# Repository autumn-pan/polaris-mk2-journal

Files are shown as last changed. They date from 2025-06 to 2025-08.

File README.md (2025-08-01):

# Lepton Rocket
The Lepton Rocket is a TVC rocket that is capable of guiding itself using its thruster, as well as vertical landing using a second thruster. It requires no parachute or fins and is capable of self-stabilization using only gimballed motors and lands propulsively.

# Motivation
Our motivation for building this rocket stems from a deep passion for model rocketry and a will to learn and improve through this project. Building such a complicated rocket not only helps us learn and grow as people but also pushes technological boundaries we face today with innovative new solutions. Every step, from Kalman filters to thrust vectoring, offers unique challenges that serve as learning experiences. We hope that our work will go on to support other aspiring rocketeers through open sourcing and tutorials. Moreover, we are testing new methods of reversing exhaust jets and are testing materials in extreme environments. We hope that this research will inspire other projects that can make a real impact.

# Design
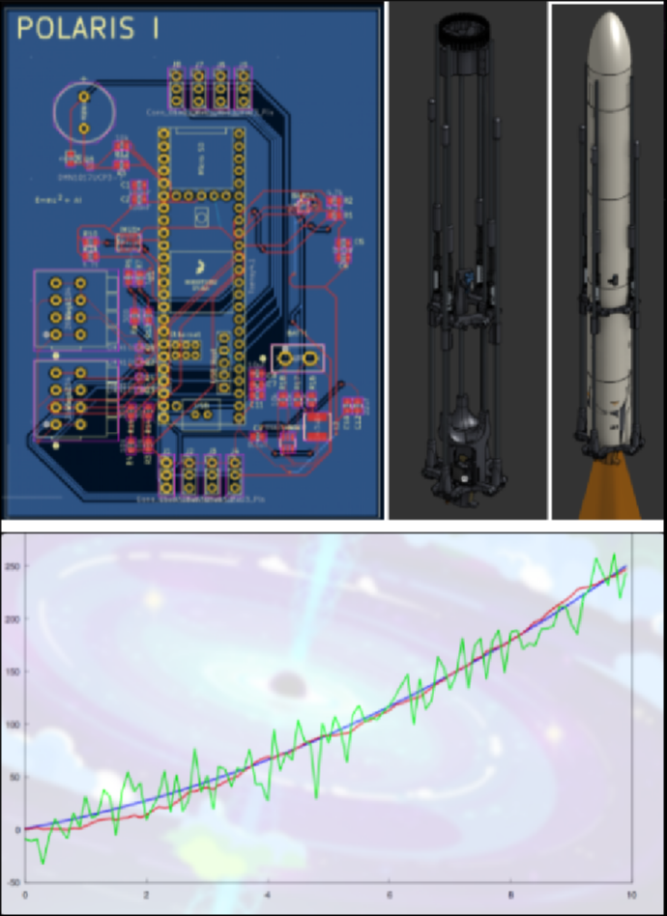
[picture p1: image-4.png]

PCB
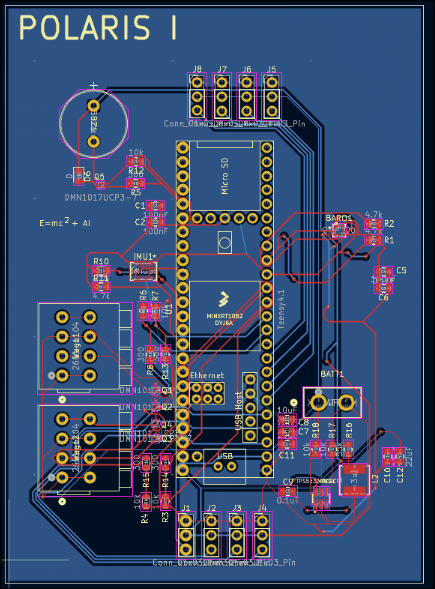
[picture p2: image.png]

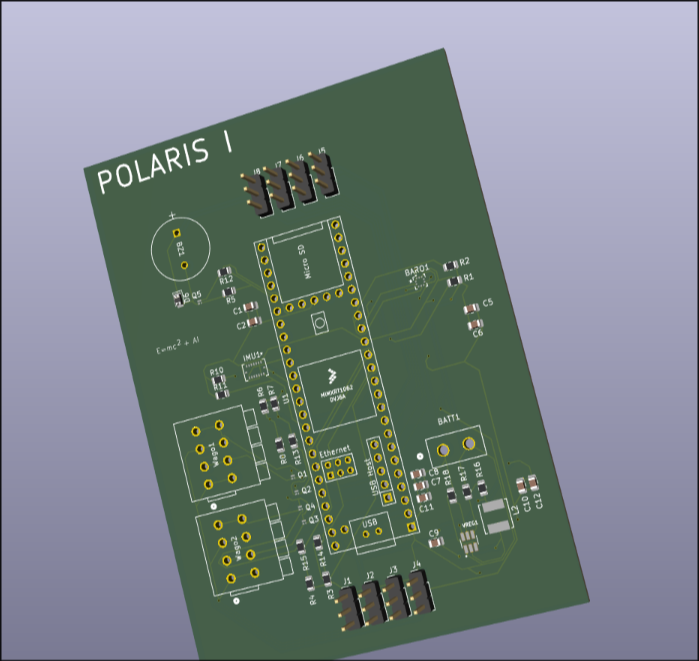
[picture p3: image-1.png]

WIRING
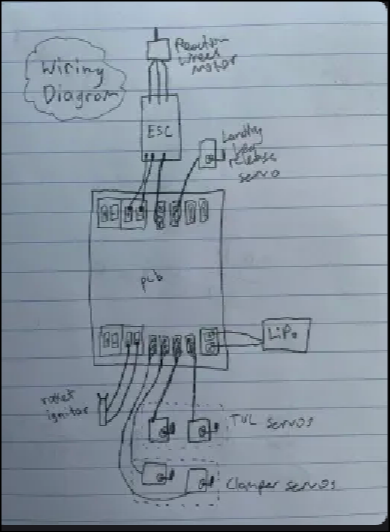
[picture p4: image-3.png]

CAD


# CAD Files
View the CAD files in ./cad, or preferably in the onshape document
[Link](https://cad.onshape.com/documents/b936ec593d2f13f8b4301d6a/w/959d82f8ce1a388125efc6ac/e/d0e27454aa34d56363c8f698)
# BOM -- Total Cost: $288.5, $307.25 after tax
| Name | Cost | Link | Purpose |
|---|---|---|---|
| Teensy 4.1 | 35.49  | [Link](https://www.amazon.com/PJRC-Cortex-M7-Processor-iMXRT1062-Without/dp/B088JY7P2H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) | Processing information and running code |
| Bosch Sensortec BMI088 | 5.23 | [Link](https://www.digikey.com/en/products/detail/bosch-sensortec/BMI088/8634936) | Reading inertial data |
| Bosch Sensortec BMP390 | 3.15 | [Link](https://www.digikey.com/en/products/detail/bosch-sensortec/BMP390/16164577) | Reading altitude |
| 2 WAGOs  (2601-1104) | 8.72 | [Link](https://www.digikey.com/en/products/detail/wago-corporation/2601-1104/17123797?gQT=1) | Connecting pyro channels |
| XT30U connector | 0.72 | [Link](https://www.tme.eu/en/details/xt30upb-m/dc-power-connectors/amass/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) | Connecting the battery |
| 8x Servo Pins (G800W305018EU) | 7.84 | [Link](https://www.digikey.com/en/products/detail/amphenol-icc-commercial-products-/G800W305018EU/13683151?gQT=1) | Connecting the servo pins |
| 5x DMN1019UVT-7 | 4.10 | [Link](https://www.digikey.com/en/products/detail/diodes-incorporated/DMN1019UVT-7/5126835) | Controlling pyro channels |
| Printed Circuit Board | 50.00  | [Link](https://jlcpcb.com/) | Mounting flight computer devices on. We only ask that you pay for printing, shipping, and taxes on the raw circuit boards. We will try to fund the resistors, capacitors, etc. ourselves |
| 3ml Syringes | 2.93  | [Link](https://www.aliexpress.us/item/3256806328171497.html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) | Dampening landing legs |
| Brushless Motor | 0.99 | [Link](https://www.aliexpress.us/item/3256806626806030.html?) | Driving the reaction wheel |
| Extension Cable | 5.99 | [Link](https://www.amazon.com/FLY-RC-Connector-Extension-Brushless/dp/B0B12CFKNZ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) | Connecting the motor to the flight computer |
| Set Screws 50pc 2cm 5mm | 1.38 | [Link](https://www.aliexpress.us/item/2251832795980382.html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) | Weighing down the reaction wheel |
| 1/4 acetyl copolymer rods-- 4 3ft rods and 8 2ft rods| 36.91 | https://buyplastic.com/delrin-acetal-copolymer-plastic-rod/ | Landing legs and supporting the fuselage
|2 servos bms127wv+| 54.97|[link](https://www.redwingrc.com/product.php?productid=2746)| Pricy, but very necessary due to the high forces that they will be subjected to. These are for tvc
| 2 servos PTK 7462W MG| 19.44 | https://www.aliexpress.us/item/3256807624830309.html? | Thrust reversal system
| TSP563200DDCR | 0.90 | https://www.digikey.com/en/products/detail/texas-instruments/TPS563200DDCR/5034343 | converting the battery to a lower voltage for the teensy to handle
| 5x 300 Ohm Resistor RC0402JR-07300RL| 0.50 | https://www.digikey.com/en/products/detail/yageo/RC0402JR-07300RL/726461 | Managing MOSFET gates
| 7x 10k Ohm Resistor RC0402JR-0710KL| 0.70 | https://www.digikey.com/en/products/detail/yageo/RC0402JR-0710KL/726418 | Pull down resistors for MOSFETS
| 4x 4.7k Ohm Resistor RC0402JR-074K7L | 0.50 | https://www.digikey.com/en/products/detail/yageo/RC0402JR-074K7L/726477 | Sensor stack pull down resistors
| 1x 55k Ohm Resistor ERA-2AEB563X| 0.10 | https://www.digikey.com/en/products/detail/panasonic-electronic-components/ERA-2AEB563X/1706047 | Managing TSP563200 output voltage
| 7x 0.1 uF Capacitor CL05B104KP5NNNC | 0.56 | https://www.digikey.com/en/products/detail/samsung-electro-mechanics/CL05B104KP5NNNC/3886660 | smoothing voltage
| 2x 22 uF Capacitor | 0.05 | https://www.digikey.com/en/products/detail/murata-electronics/GRM188R61A226ME15D/5027561 | Smoothing voltage with the TSP
| F15-0 Estes Rocket Motor| 22.95 | https://fusionscalehobbies.com/products/estes-f15-0-29mm-engines-2pk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 | Launching the rocket |
|Solder paste | 4.36 | https://www.aliexpress.us/item/3256809207808464.html? | soldering SMDs to the PCB |
| Threaded inserts | 1.73 | https://www.aliexpress.us/item/3256803396040989.html? | TVC assembly |
| Bearings | 6.26 | https://www.aliexpress.us/item/3256802138888272.html? | TVC Assembly |
| 5x Threaded acrew | 7.05 | https://www.aliexpress.us/item/3256806603708402.html? | General connections |
| Insert Nuts | 4.98 | https://www.aliexpress.us/item/3256808011211144.html? | General connections |

Notes on our vendors:
- Teensy 4.1 is necessary for its high speed, reliability, and ease of use. It is necessary for advanced avionics like this project. However, it's difficult to optimize the price of, and the cheapest price from a trusted vendor was about $31. Considering free shipping however, the cheapest vendor was on Amazon and was $35. Aliexpress was thoroughly considered and while vendors there were considered, they were found to be misleading and/or untrustworthy. A bad MPU is not only a waste of money and time, but can also be a violation of safety guidelines.
- The acetyl copolymer rods are the cheapest and most reliable on the market for what they are-- we thoroughly checked. Aliexpress does not offer any rod long enough to support this rocket, and has insufficient quality assurance which could compromise the safety of this project. Also note that this is including shipping for a large object, which is absolutely necessary in this case. Alternative rocket bodies can cost upwards of $90 at this size, so this really is the cheapest possible. Furthermore, we considered carbon fiber rods from aliexpress, however we were not allowed to purchase them in the quantity that we needed, and even the cheapest rods from Aliexpress did not make a significant difference. We really optimized the rods and rocket body to the extreme.
- We looked on Aliexpress for banana extender cables, but all options were either more expensive or significantly too short for what we needed. The one on amazon is the cheapest one that works.
- The servos we found are the only servos strong enough that can fit inside the rocket. Any larger servos could introduce significant problems during flight. These are also necessary because it is for a guidance system, and therefore needs to be fast and respond quickly. We found the cheapest servos possible.
- The servos for thrust reversing can be cheaper, so we got the cheapest servos from Aliexpress that are still strong enough to do their job. This cut costs by upwards of $40. The servos could not be cheaper than this.
- We were promised that Hack Club would supply one pack of Estes F15-0 motors by Acon
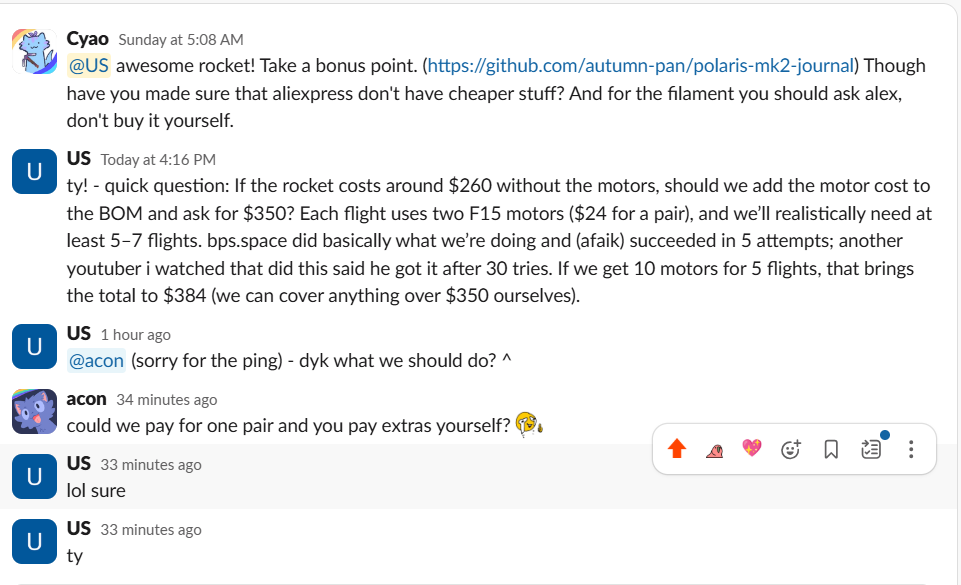
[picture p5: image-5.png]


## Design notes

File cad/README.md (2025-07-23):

Link to the Onshape:
[Link](https://cad.onshape.com/documents/b936ec593d2f13f8b4301d6a/w/959d82f8ce1a388125efc6ac/e/d0e27454aa34d56363c8f698)

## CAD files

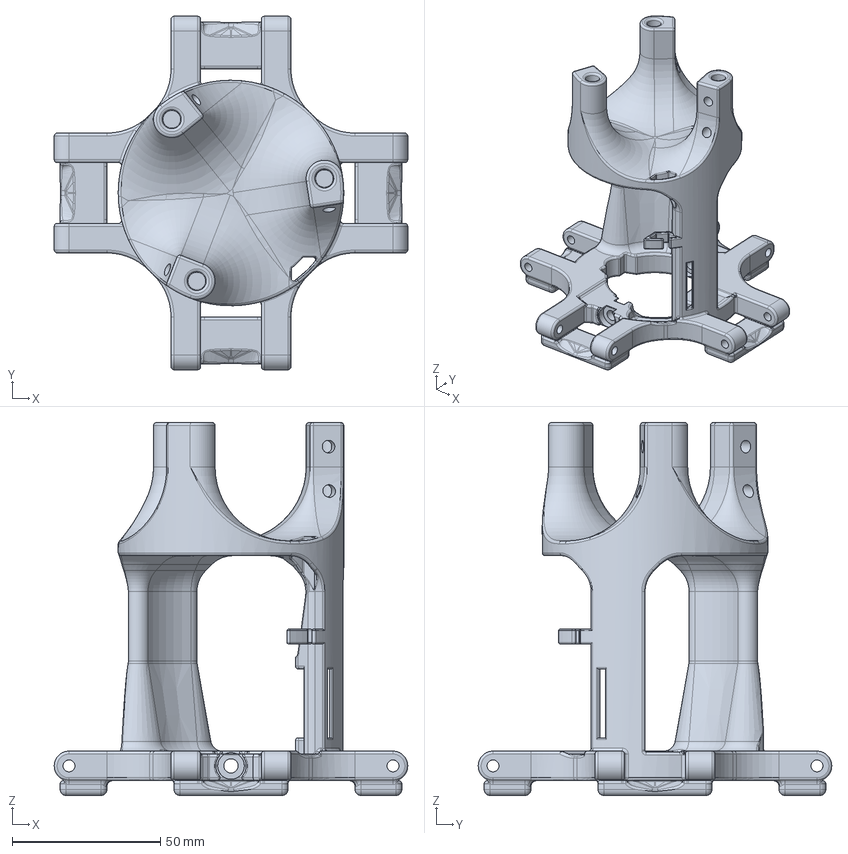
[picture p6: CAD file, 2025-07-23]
cad/Assembly - Outside.step
119.4 x 119.4 x 126.0 mm

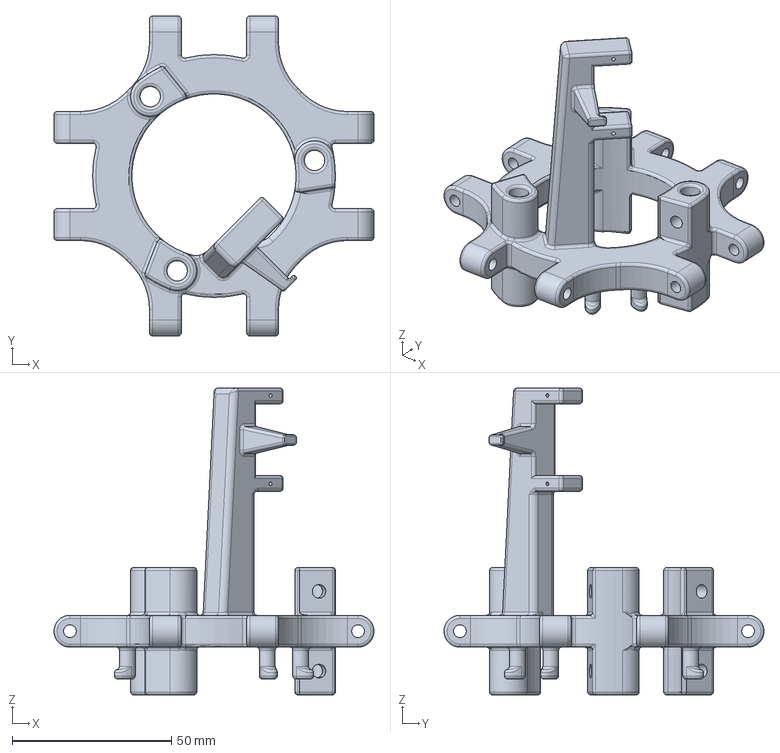
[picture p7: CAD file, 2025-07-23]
cad/Assembly - Part 23.step
100.4 x 100.4 x 96.3 mm

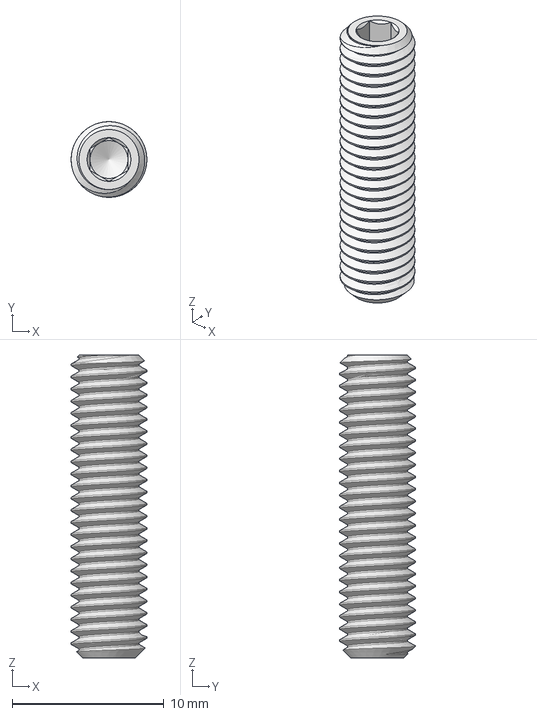
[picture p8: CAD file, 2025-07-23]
cad/Assembly - Part 1 (36).step
5.00 x 5.00 x 20.0 mm

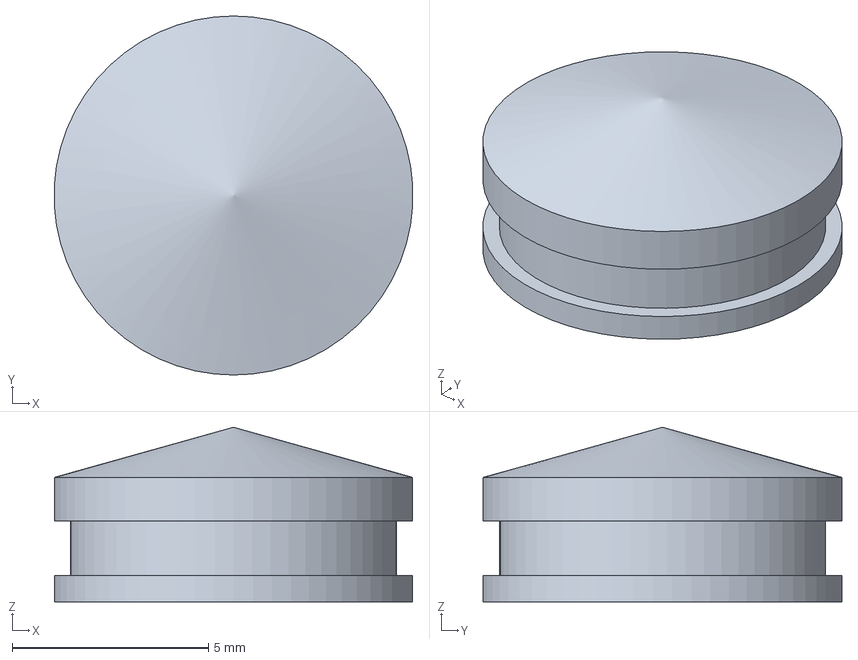
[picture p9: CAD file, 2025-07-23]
cad/Assembly - 7510A651_Plastic Syringe (11).step
9.13 x 9.14 x 4.45 mm

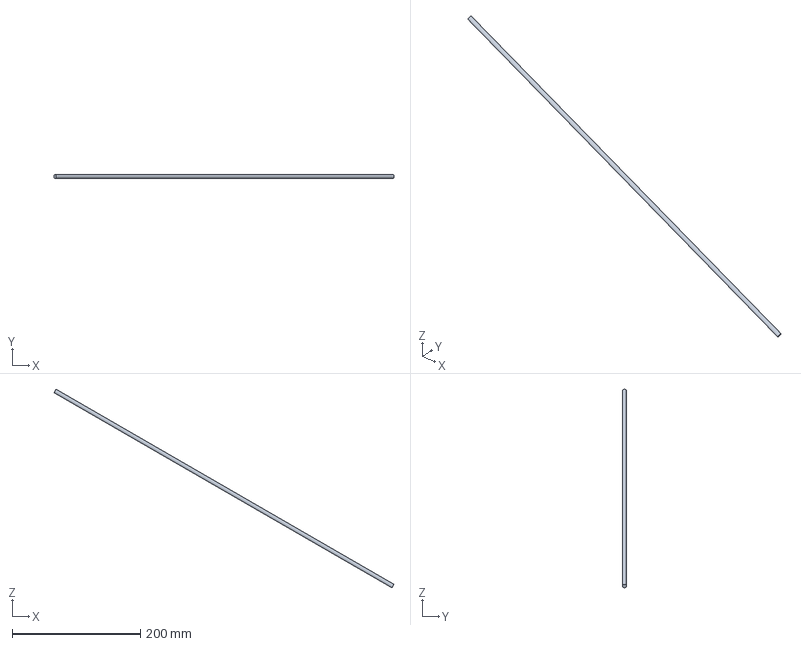
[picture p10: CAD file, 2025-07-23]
cad/Assembly - Part 21.step
531.1 x 6.35 x 310.3 mm

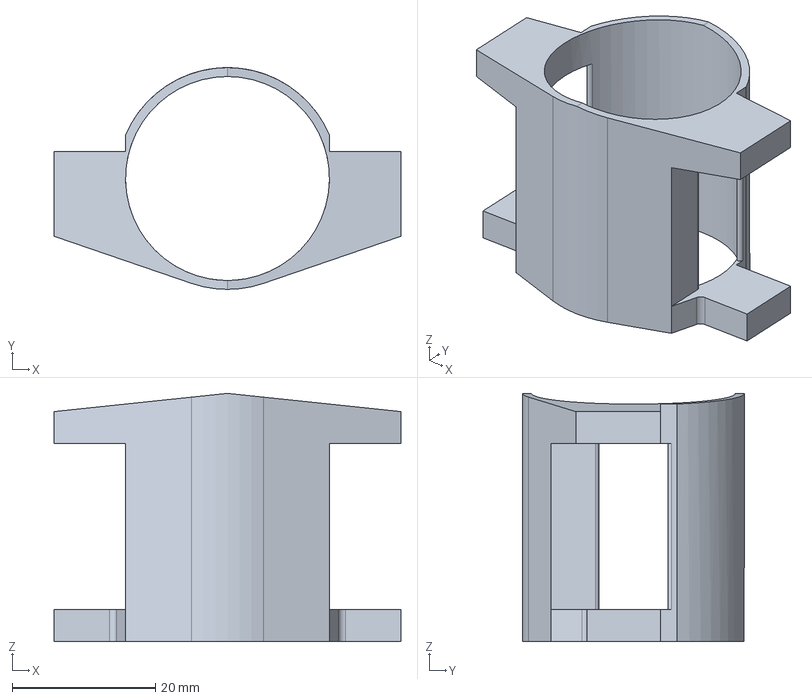
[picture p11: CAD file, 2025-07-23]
cad/Assembly - Part 8.step
48.5 x 31.0 x 34.7 mm

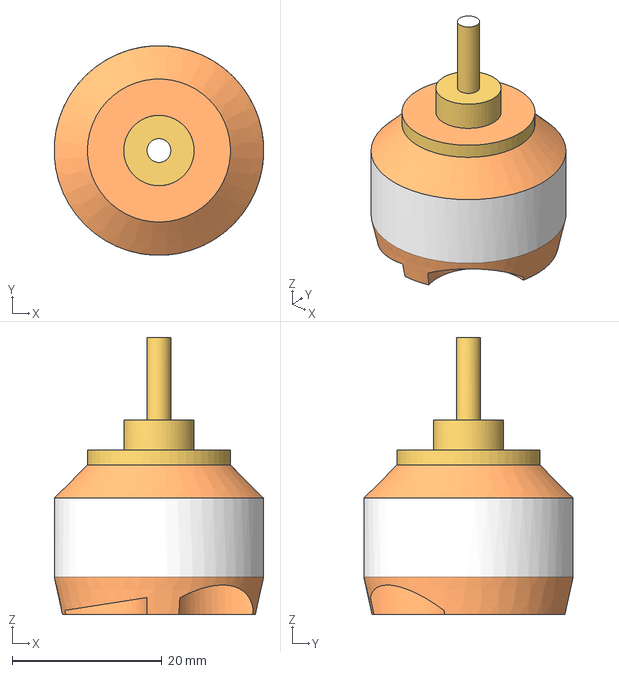
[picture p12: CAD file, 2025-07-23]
cad/Assembly - DYS D2822 2282 1100KV 1450KV 1800KV 2600KV Brushess Motor.step
28.0 x 28.0 x 37.0 mm

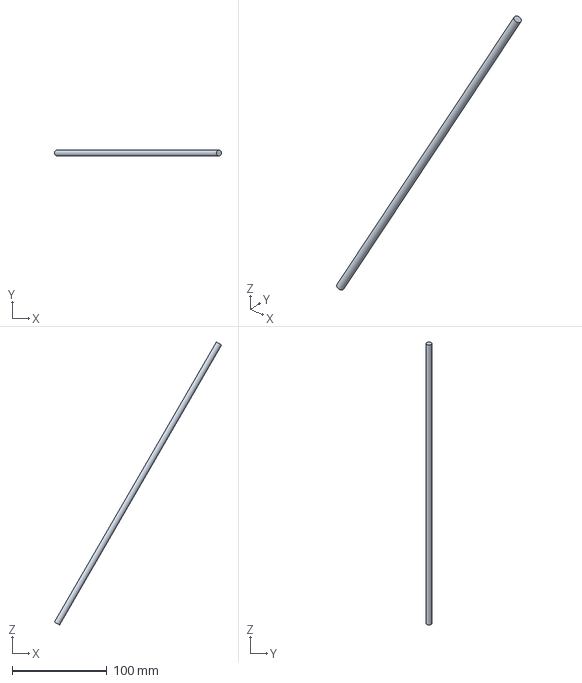
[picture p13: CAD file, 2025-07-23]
cad/Assembly - Part 26.step
176.5 x 6.35 x 298.8 mm

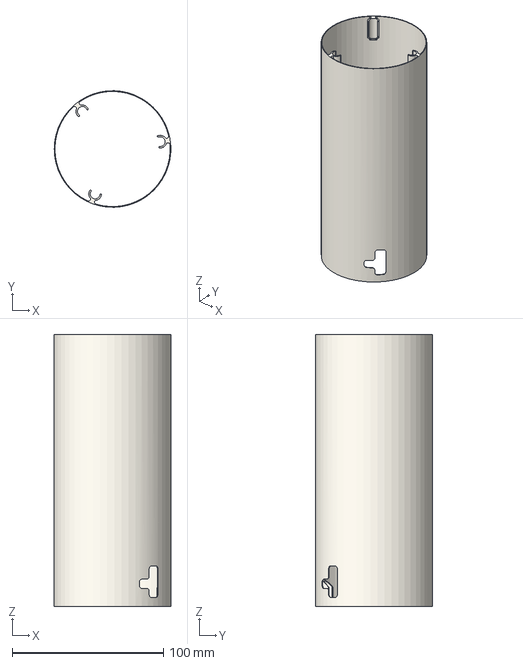
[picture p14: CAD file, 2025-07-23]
cad/Assembly - Part 31.step
77.1 x 77.2 x 180.0 mm

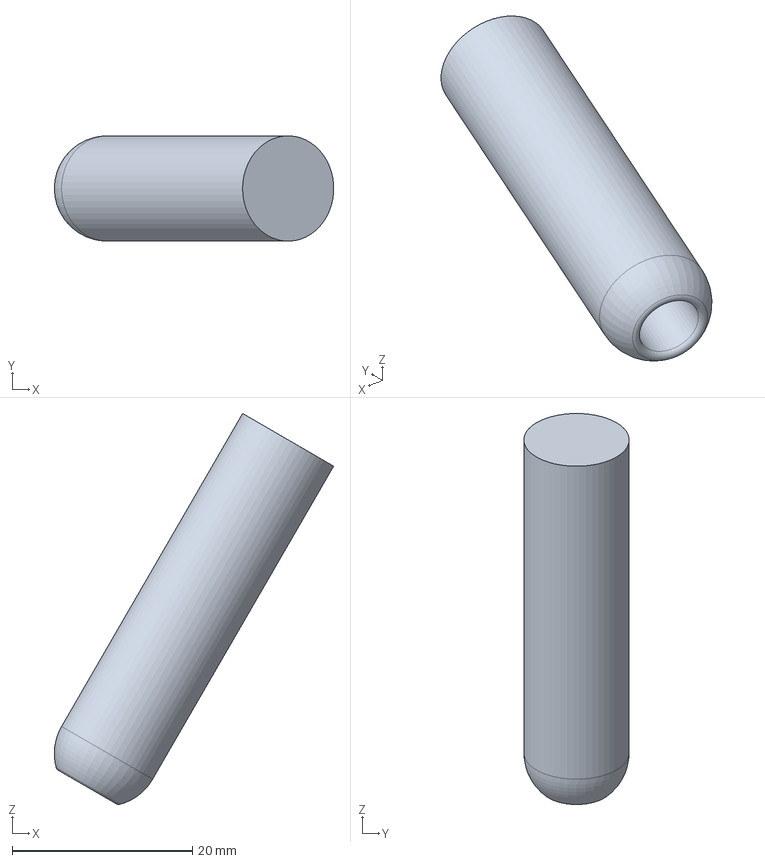
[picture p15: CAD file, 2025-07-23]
cad/Assembly - Part 25.step
31.0 x 11.7 x 43.4 mm

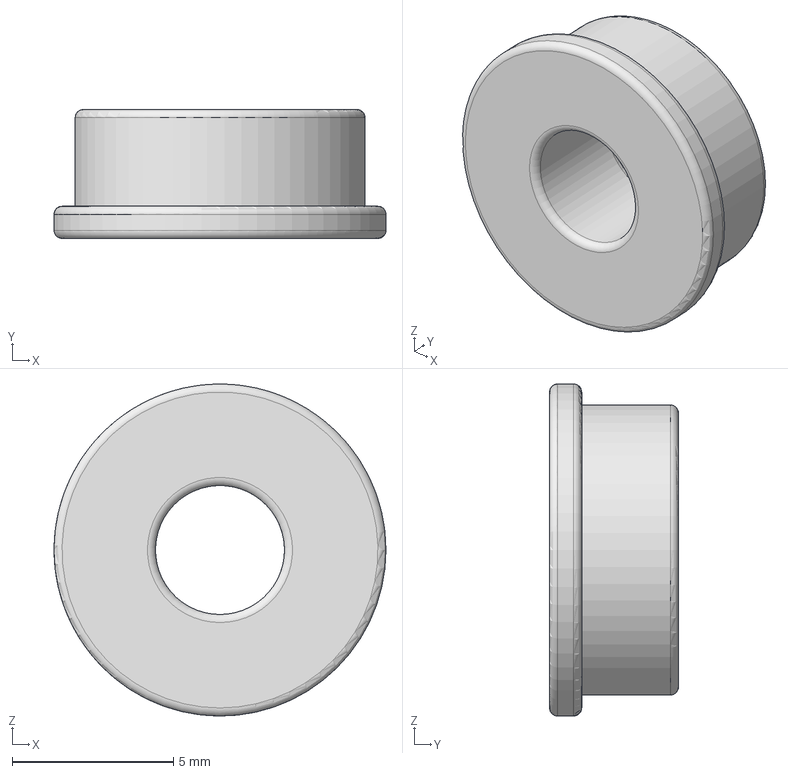
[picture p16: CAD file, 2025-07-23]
cad/Assembly - Bearing.step
10.3 x 4.00 x 10.3 mm

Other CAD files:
cad/Assembly - Part 1 (28).step
cad/Assembly - Part 1 (20).step
cad/Assembly - Part 1 (33).step
cad/Assembly - Part 1 (26).step
cad/Assembly - Part 1.step
cad/Assembly - Part 1 (27).step
cad/Assembly - Part 1 (29).step
cad/Assembly - 7510A651_Plastic Syringe (1).step
cad/Assembly - 7510A651_Plastic Syringe (10).step
cad/Assembly - 7510A651_Plastic Syringe (2).step
cad/Assembly - 7510A651_Plastic Syringe (3).step
cad/Assembly - 7510A651_Plastic Syringe (4).step
cad/Assembly - 7510A651_Plastic Syringe (5).step
cad/Assembly - 7510A651_Plastic Syringe (6).step
cad/Assembly - 7510A651_Plastic Syringe (7).step
cad/Assembly - 7510A651_Plastic Syringe (8).step
cad/Assembly - 7510A651_Plastic Syringe (9).step
cad/Assembly - 7510A651_Plastic Syringe.step
cad/Assembly - BMS-127WV (1).step
cad/Assembly - BMS-127WV (2).step
cad/Assembly - BMS-127WV.step
cad/Assembly - Bearing (1).step
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

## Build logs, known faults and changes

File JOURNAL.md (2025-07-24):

---
title: "Lepton Rocket"
author: "Umit Selvitopu/Autumn Pan"
description: "An F-Class propulsively landing rocket"
created_at: "2025-5-21"
---

Autumn Pan -- Lepton Rocket Logs -- Approx 104 hours
PCB, Code, and Design

# Day 0, May 21
When the rocket lands, it may still have a lot of kinetic energy, which is why we need landing legs with shock absorbers. Today we discussed what shock absorbers to purchase and settled on ones from McMaster.

I read through kalmanfiltertutorial among other sites to gain a rough understand of a kalman filter, which will be used later on to sort out sensor noise. I was walked through the alpha-beta-gamma filter and learned about multivariate gaussians. It was quite challenging to understand, but a kalman filter is essentially a recursive algorithm that takes the weighted average of different equations and sensor readings to determine to the best of its ability, the state of your rocket.
Time spent: 4hr
# Day 1 May 22
Before I work on Polaris Mk. 2, the flight computer on the actual rocket, I want to create the groundwork for this project by first writing a simpler flight computer so that I can better plan for this one. I initialized a PlatformIO project and imported the necessary libraries. I started out by removing unnecessary code from main.cpp. Then, I imported the BMP390 Barometer and BMI088 IMU. These two sensors will be used to find the position, velocity, and orientation of the rocket, which is important for nearly every maneuver. Of course, sensors aren't perfect so I'll have to implement something called a Kalman filter later on. I finished a very primitive version of a sensor handler class. Total time spent: 1hr
# Day 2 May 24
The first thing I did today was finish up implementing the barometer so that I could measure altitude. This also requires sea level atmospheric pressure to calculate, which varies from place to place. I decided to have it stored dynamically rather than hardcoded. A pyro channel is a pin meant to ignite a pyrotechnic device, which usually require higher voltages. I created a PyroChannel class that can fire a pyro channel for some duration, which can be used for things like parachute deployment or a second stage. I researched the Arduino SD library so that I could implement an SD card class for logging information, like sensor readings. Also, I realized that I should be storing the values of the sensors each cycle rather than directly getting them from the sensors because its more efficient, so I switched to that. Total time spent: 2.5 hrs
# Day 3 May 25
One of the bigger changes I made today was completely overhauling the SDCard class into the Logger class, which is now capable of organizing logs, along with other capabilities. I added header guards to Pyro.h to prevent any redefinition errors because I forgot to add them yesterday. I also realized that I forgot to license my work, so I did so under the MIT license. I also added a class to handle keeping track of time, which offers utils like last cycle time and elapsed time. TIme spent: 1.5 hrs
# Day 4 May 26
This was the day when I finally implemented the Kalman filter. So, when you try to use sensors, they will always have some amount of noise which can give you innaccurate readings. The goal of the kalman filter is to minimize this noise as much as possible to create the most accurate guess of the rocket's state as possible. I implemented this by using the C++ Eigen library for linear algebra and following the kalman filter equations. I derived my own state transisiton matrix, which essentially integrated acceleration and velocity. I decided not to kalman filter my gyros because I thought that it would be uneccesary for such a short flight and would increase cycle time. Then, I merged this branch into main. Total time spent: 4 hrs
# Day 5 May 27
Today I began testing for my kalman filter. I used my statesim project, which modeled kinematics and sensor noise, to test this. I imported my kalman filter and deps, then I learned and installed matplotplusplus to graph the information. Immediately, I found that my kalman filter did not function correctly and outputted nan, which I fixed by removing some zeroes from the covariant matrices. Next, the kalman filter was off by orders of magnitude, which was the result of an upside-down state transition matrix. Finally, I managed to get it to work at just over 50% reduced noise compared to raw sensor data.

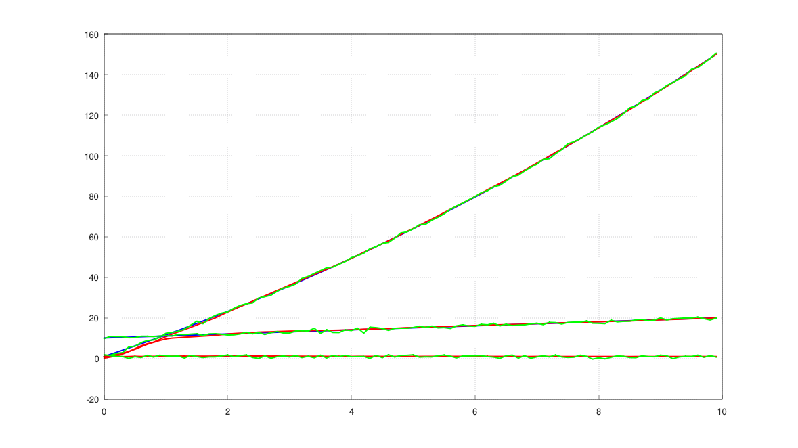
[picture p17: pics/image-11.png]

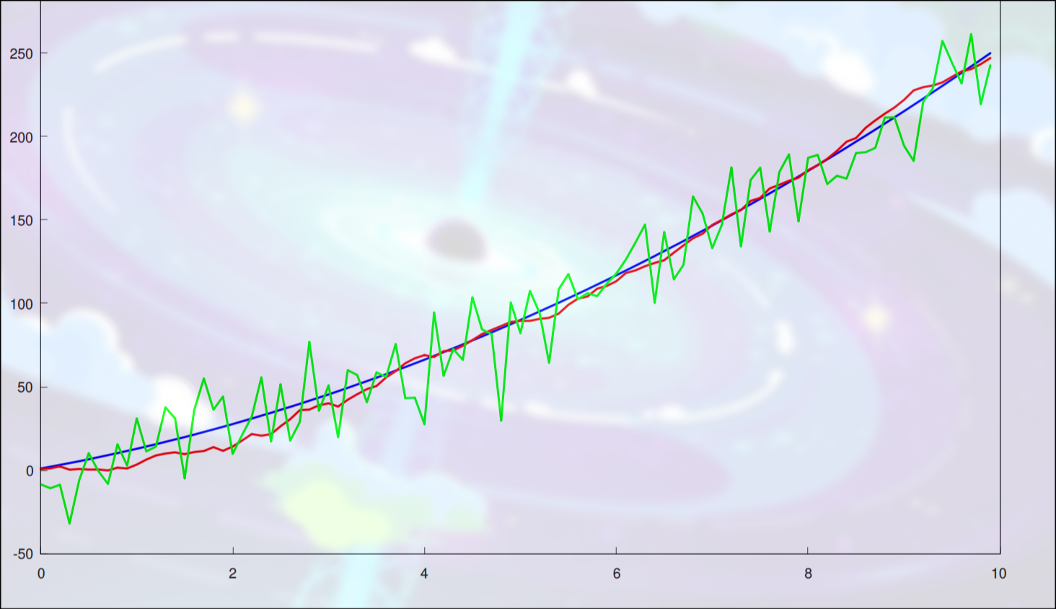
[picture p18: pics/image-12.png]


Total time spent: 6 hrs
# Day 6 May 28
Today I learned and tested a complimentary filter, which was difficult to tune. It ended up being around 60% the effectiveness of a kalman filter. It runs more efficiently with less instructions to the MPU, but I have a teensy 4.1 so it won't matter. I'll stick to the kalman filter because its simply more effective and I can handle the extra strain.
Time spent: 4hr
# Day 7 May 30
However, when I ran the filter for 10000 cycles, things started to break down. I first switched the filter to using doubles instead of floats, which decreased noise by 20%. Then, I set dt = 0.005 to simulate real cycle times. This brought the kalman filter back to normal. I set the filter to run for 1000 cycles with cycle time 5ms, and got this result:

The kalman filter was ten times better than raw sensor data. Since the noise has actually been extremely exaggerated this whole time, and I still managed to get the kalman filter to +- 3 cm, this will be more than enough during flight.
Total time spent: 1hr
# Day 8 May 31
Today I learned KiCAD and started writing the schematics for the Polaris II flight computer that will be used for this rocket. It has 3 pyro channels, 2 BMI088 IMUs, and a BMP390 Barometer. The pyro channels will be used to fire ignitors for tasks like stage separation and deploying the landing legs. I chose the BMI088 because of its low cost, high precision, and its ability to handle impacts. Although I considered the BMI270 for its extremely low power consumption, the difference was negligible in my case because I am using nice LiPo batteries which is more than enough. The BMP390 was the most precise barometer I could find for this project, with its altimeter being +- 0.1m. This is amazing, and will be further improved when coupled with my kalman filter. Today however, I mainly worked on learning how to use KiCad and importing the necessary libraries. I also made the schematics for the BMI088

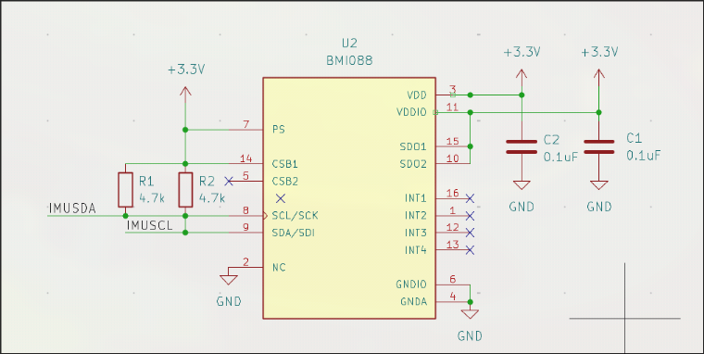
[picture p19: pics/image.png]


I also labeled some pins for the MPU

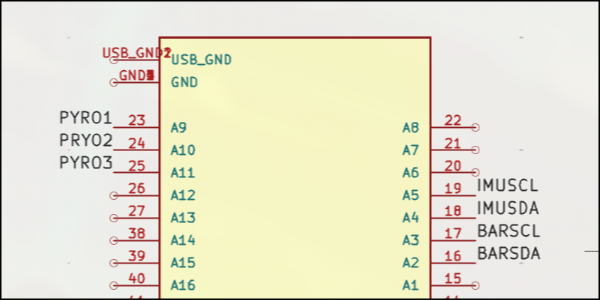
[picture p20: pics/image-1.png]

Time spent: 4hr

# Day 9 June 01
Today, I didn't work much because of excessive homework. However, I did do a lot of research about pyrotechnic channels and looked for nice screw terminals. Here's my progress today:
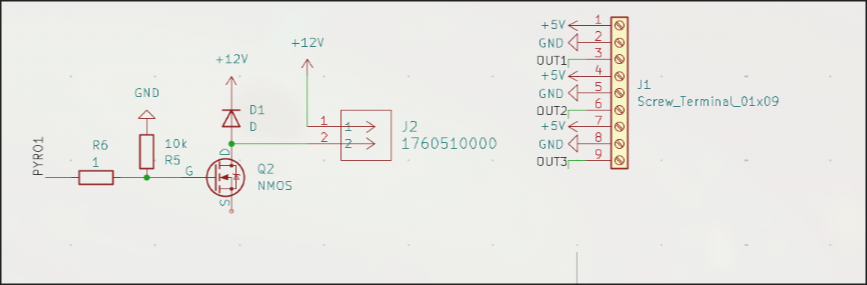
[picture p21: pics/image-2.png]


I mostly analyzed other schematics to learn more about best practice. The diode is to help protect against things like reverse polarity. I used an N-MOSFET to push 12v into a screw terminal, which will be used to activate any pyrotechnic devices. I used a 10,000 ohm resistor which will make it much safer. I also set up some stuff for general output stuff which will be used to run the 5 servos we're using.

Time spent: 2.5hr
# Day 10 June 02
The first thing I did was attempt to draw the schematics for the battery.
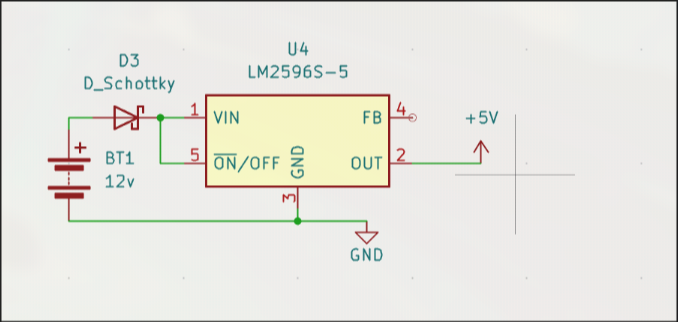
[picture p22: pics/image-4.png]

It uses a buck converter to convert 12V to 5V. I used a Schottky diode to help protect against reverse polarity. It will probably cause some amount of voltage drop, and I'm unsure at the current moment what the consequences of that will be. That's it for the battery. I then implemented an LED which is self explanatory:
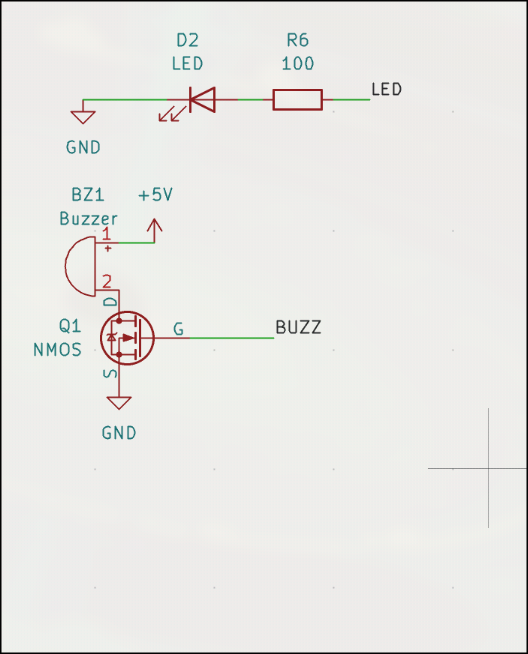
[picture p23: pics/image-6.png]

On the bottom is a piezo buzzer(?) and it is controlled using an N MOSFET because it needs 5v instead of the supplied 3v.
Time spent: 2hr

# June 07/08/09 (Offline Work)
These two weeks, I am between studying rigorously for finals and relaxing for the first week of summer break. However, I did do some calculations during this time. I know that mass will be lost over time as fuel burns, and it wont be linear. I assume that the thrust curve of a rocket motor corresponds to mass lost over time roughly, so I derived approximation formulas, first linearly. I used multivariable optimization to do so, and moved to nth degree polynomials. It was around this time that I became aware of Runge's phenomenon, but I'll consider that later. If I can approximate the curve well, then this rocket will have more accurate information.
Time spent: 2,2,1hr

# Day 11, June 20
I added a state detection system which can detect apogee, launch, and landing. It does so by storing the filtered velocity and comparing it this certain thresholds to get an idea of the true velocity. If the velocity is suddenly negative, that means that its falling and has theefore just passed its apogee. Likewise, if it suddenly spikes upwards, then it has launched. If it is suddenly close to zero, then it has landed. It checks this every cycle to deterine the state of the rocket with a few ms of latency.

Time Spent: 2 hr
# Day 12, 13, 14, June 21, 23, 24 (Research Days)
I spent a significant amount of time away from the codebase and instead researching real time operating systems. Polaris I does not use an RTOS, and instead employs a super loop, where all necessary functions are called each cycle

A scheduler is much more sophisticated than this. While a super loop can get held up in a sort of traffic, namely less important tasks taking a long time to execute and blocking crucial tasks, schedulers carefully manages task execution and crucially allows for multitasking. However, a scheduler is much more complex than a super loop and has some overhead. I may not even have to time to implement a full scheduler so I will continue working on other subsystems and see what opportunity I have. One of my greatest concerns however, is that of logging. Apparently logging can take a significant amount of time and this could block or delay things like TVC or the kalman filter from working in time, and could cause performance issues without some sort of scheduler.

Time spent: 3,2,3 Hours

# Day 15 June 26
I spent most of today looking through my code and for errors. One particular bug that I had known about was one with the logger, where I would log important events and sensor information together in one file, which is a bad idea if you're trying to graph anything. I split the logging into two simultaneous files. This may raise some performance concerns, but we'll deal with those ones the flight computer is actually built.

Also, I added a way to get the full state vector in one method call directly from the kalman filter which could be useful for slightly faster execution times for updating flight computer information.
Time Spent: 1.5hr
# Day 16 June 27
I added a simple Motor class in preparation for a mass tracking class. I planned out a new class that would track the mass of the rocket over time, as fuel is burnt and parts are jettisoned. THe motor class is a significant part of this, as it tracks the propellant mass over time and more useful information about the rocket.
Time Spent: 1hr
# Day 17 June 28
I added a significant amount of logic to the Motor class such that it is entirely operational. I added further information that is handled by the class, such as whether or not it has been jettisoned. Propellant burn rate and getter functions were also added today. I made changes to the flight computer's handling of rocket state information too.
Time spent: 1hr
# Day 18, July 1
The first thing I did was clean up the kalman filter, as it had redundant and dead code that could be removed for faster execution time. I also implemented logic for the MassTracker class. I handles both rocket motors which will be used for ascent and landing, and carefully tracks the mass of each one. To save computation time, I decided to assume a constant mass flow rate instead of utilizing the calculations I did last month. I fixed some typos in the logger, and changes the Motor's update function to return boolean values, inspired by Java's standard libraries. This change gives information on whether or not the rocket has burned out.
Time spent: 2hr
# Day 19 July 2
Today I tried to make a scheduler. It will split tasks into small chunks and alternate quickly between working on each task. I added a lot of ways to rearrange the order of tasks. Tasks are currently stored in a vector, and I added ways to add, remove, set, swap, etc. tasks. Their order in the vector denotes their priority. This will hopefully do a lot against blocking tasks like logging, which is low priority. Another important thing I set up was the Task class which contains an execution interval, a function, and a start delay. These determine when and how often the task executes in the scheduler.
Time spent: 1.5hr
# Day 20 July 3
I continued to work on the scheduler, and added more logic and implemented a lot of the utility and getter functions, particularly surrounding the task vector. I set up constructors for the new classes and realized I was on the wrong git branch. I subsequently merged everything over to main.
Time spent: 1hr
# Day 21 July 4
I added comments to my code and added checks to ensure that all of the information in the scheduler was up to date, as certain changes to task priority could mess that up.
TIme spent: 30m
# Day 22 July 5
I realized that the scheduler would be too complex to fit into this project in time so I move everything to the scheduler branch and switched the main branch back to a super loop.
Time spent:20m
# Day 23 July 6
Today I reviewed the kind of information that I would require post-flight for analysis. I will log acceleration, velocity, position, roll, pitch, and yaw, as well as time
I implemented these into the logger instead of the placeholder values and added proper functionality, which will allow for this to be properly graphed
Time spent: 10m
# Day 24 July 7
To track orientation, one must add it up over time. I have previously thought this would be as trivial as at + v, but I realized that it's a bit more complicated than this. I have 3 options: matrix representation, euler angles, or quaternions. Euler angles are simple but have gimbal lock, and quaternions are computationally lighter than rotation matrices, so I went with quternions. First, I read up on quaternion integration, as that would be how I add angles. I added a Quaternion class and defined multiplication, scaling, and addition. Tomorrow, I will add quaternion integration.
Time spent: 2.5h
# Day 25 July 9
I first added vectors. This is generally useful because angular velocity can be represented as vectors, and there is a vector component of each quaternion. I only defined addition, subtraction, scaling, and dot product, as well as norm/magnitude. These are the most fundemental operations that I need for this class to be useful in the context of rocketry.

I then added quaternion integration. More specifically, I defined an exponential mapping. I also added quaternion normalization and magnitude. the exp of a quaternion is vital for integrating it optimally without numerical errors. I also looked into taylor expansion. The taylor series is a method in calculus for expanding transcedental functions into simple series, and can be used to represent trigonometric functions like sine and cosine. For smaller angles, I might be able to get away with a simple taylor expansion with a few terms to save on computation time. This stayed on paper, but I sriously may implement this later. It would decrease accuracy but increase computation time.

Time spent: 2.5hr
# Day 26 July 10
Today I implemented the previous mathematical framework I had just created using the new RotationHandler class. The main part of this class is that it integrates quaternions using the formula

 (exp(0.5angVel dt) Q)

 The RotationHandler also takes gyro values directly from the sensors as there's no real need for a kalman filter at these scales of operation time. Drift wont be too significant, hopefully. I also made a quick function to convert cartesian angles to quaternions if needed.
 I also found a potential memory leak, so I fixed that too.
 Time Spent: 1hr

 # Day 27 July 12
 First thing I did was add the rotation handler to the flight computer, so orientation is now being actively tracked. I then, based on the previous scheduler I made, created a new kind of tool for handling tasks. It cycled between doing different tasks, completing one on one cycle and the other on the next in a sort of cycle. This was the TaskCycler class and it helped spread out logging into two different parts that would each take up less time per cycle. This means that important things like rocket controls will be allowed to do their jobs in time. I also added much of the old functionality of the scheduler such that this TaskCycler is very easily configurable in the list of tasks.
 Time Spent: 1.5hr
 # Days 28-29, July 15/16
 I worked a lot of planning and the PCB. I redid the schematics for both of the sensors, redid the pyro channels, and switched to a new converter. I readded LEDs and a buzzer. I also switched to a real MOSFET. I also switched from screw terminals to WAGOs. The electronic schematics were essentially overhauled.
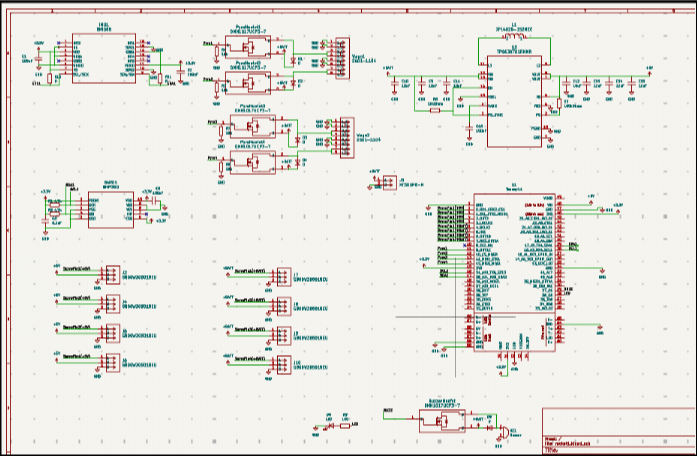
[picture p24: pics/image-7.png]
 

The rocket will of course have propulsive landing. To do this, I will have thrust reversers that can essentially cut off thrust on demand. This is how I will throttle a solid rocket motor. However, few materials can survive that kind of environment. For a while, that material has been graphite. Although it is abrasive and soft, it can survive extreme temperatures. Recently however, a new material has come up: high temperature reinforced aerogel. This can survive well above the necessary temperatures and advertises that it can be used in high stress environments too, like industrial furnaces. The specific product is SHT1300. Aerogel has excellent thermal shock resistance and low conductivity from my research, so this would be idea. I thoroughly researched this new material, and came to the conclusion that although it is an excellent insulator and a solid option, the short burn time could actually be endured by something like stainless steel 310. It has good thermal shock resistance meaning it might not crack under the high temperatures. Furthermore, I could easily apply a thick layer of ablative coating to help protect it. If I managed to get stainless steel 310 plates, they would be a surprising ideal and very simple solution to the problem. I also made adjustments to the flight computer's code and cleaned the code to be more maintainable.
Time Spent: 5,5hr

# Day 30 July 17
I looked for others to help review my schematics so that there wouldnt be a failure later on. I chose not to create the pcb until it had been reviewed by someone else. It was pointed oiut to me that my new pyro channels were not correctly configured and would be quite problematic. So, I will look into the pyro channels tomorrow and create a working design.
Time spent: 1hr
# Day 31 July 18
I redesigned the pyro channels today.

Someone pointed out that I would need to deal with ringing, so I added 300 Ohm resistors to the gate. I added a diode for voltage spikes and switched around the mosfet. I did the same for the buzzer mosfet too.
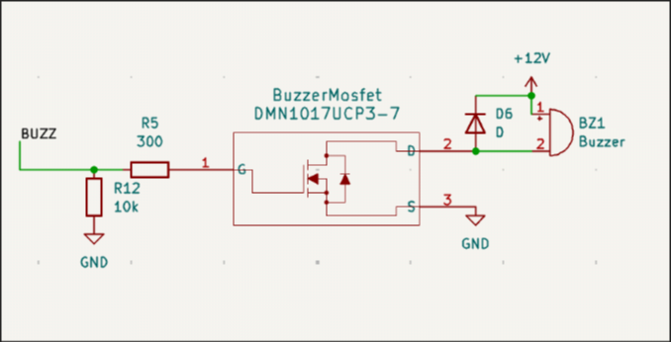
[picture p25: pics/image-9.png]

I also switched the buck converter for the battery back to an LM2596
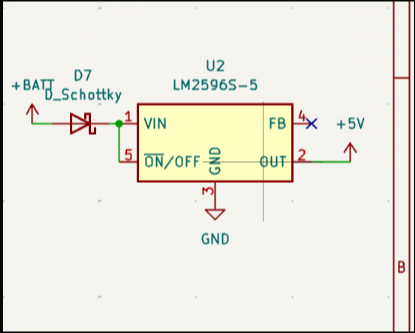
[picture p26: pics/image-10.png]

This is much easier to solder and is something I'm more confident about. It was also easier to organize, looks cleaner, and is better known. I also got these new components reviewed as well, all seems to be good.
I did review the datasheets for both buck converters considered. Furthermore, I worked on decreasing the BOM. PLA should make it a lot cheaper than the PETG we've been planning, but it might fail.

Time Spent: 4hr
# Day 32 July 20 
I switched the buck converter to the TSP563200DDCR instead of the LM2596 because it has lower noise. I spent a lot of time looking for this one, as I realized that the LM2596 was obselete and too noisy for use in this rocket. The TSP563200 should suffice instead. I spent the day working on this, and also got the pcb editor set up with every net and footprint.

Buck converter
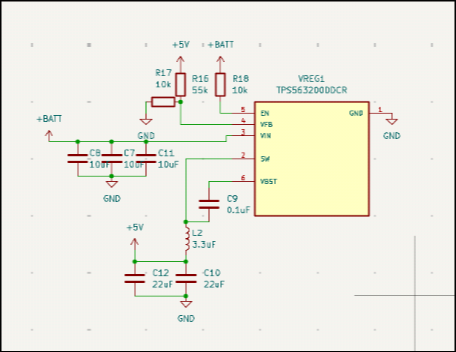
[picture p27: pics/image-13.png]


Finished schematic
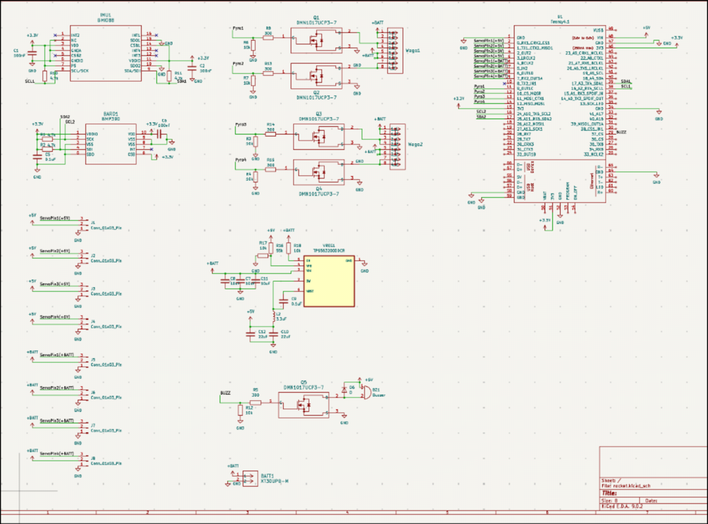
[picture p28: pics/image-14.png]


Time spent: 6hr
# Day 33/34 July 21 and July 22
I spent the day setting up the first iteration of the pcb. I was new to KiCAD PCB editor so I spent a lot of time learning to use it, and began my first draft of the PCB. After a few hours, I had this:
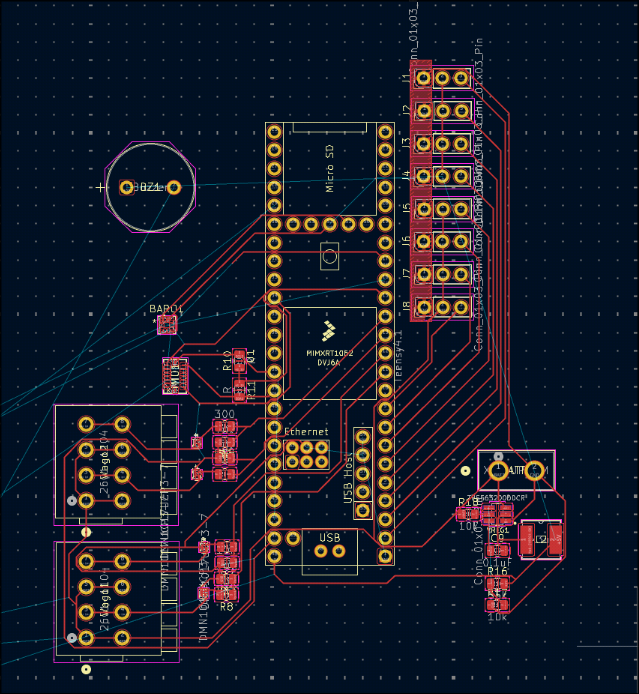
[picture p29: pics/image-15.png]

This is unsatisfactory because it's messy, too bloated, and hard to maintain, so I restarted.
End result:


This pcb layout organizes the components much better and seperates the pyro channels from the servos. There is no LED so the buzzer will serve as a way of debugging code. I added some silkscreen text as well.

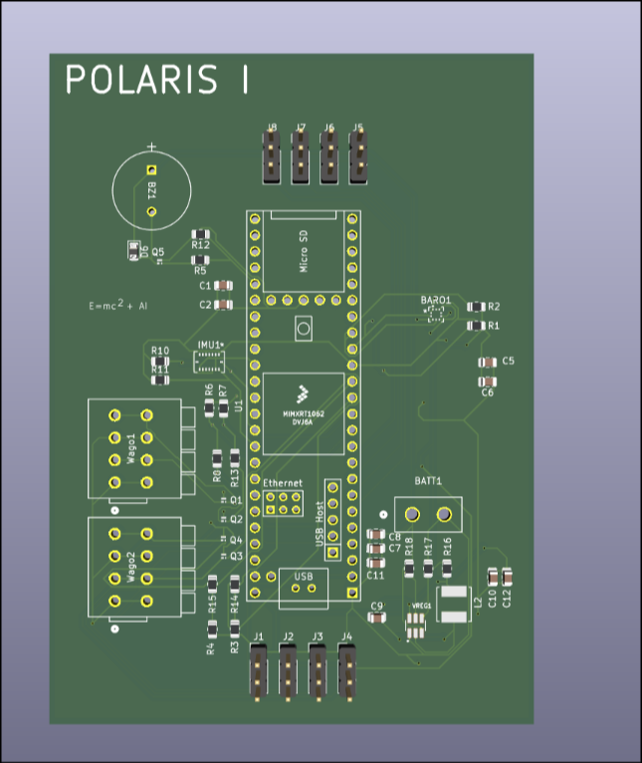
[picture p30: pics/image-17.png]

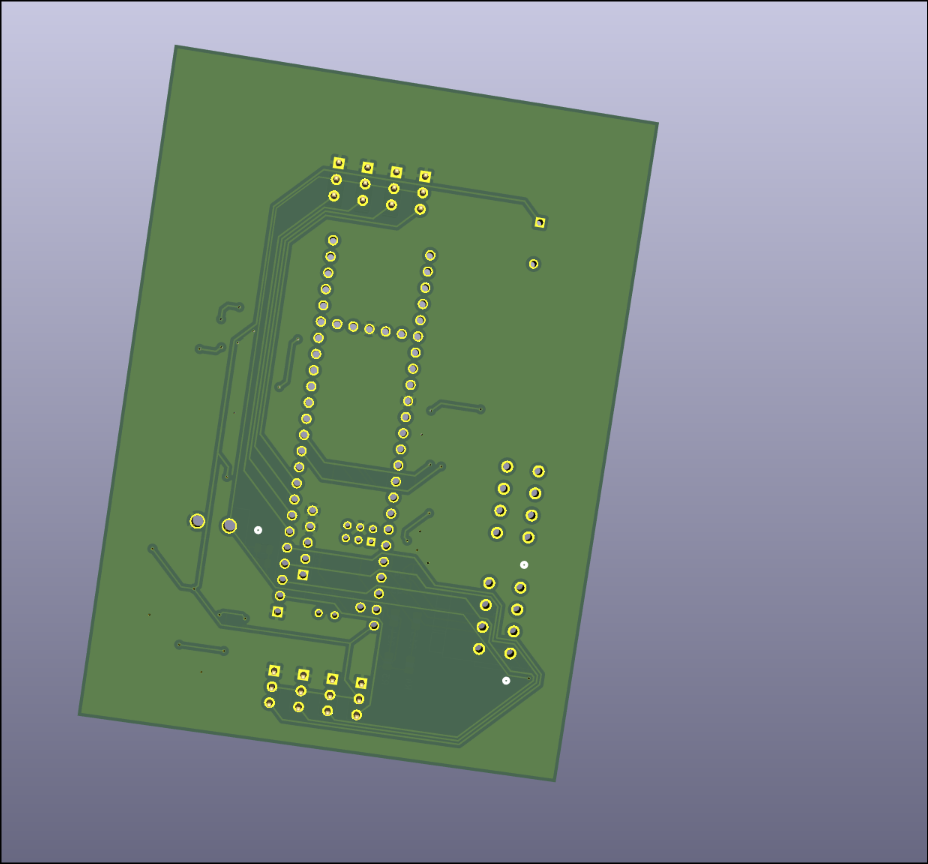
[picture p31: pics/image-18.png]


In the end, I'm quite happy with now this pcb turned out.
Time spent: 13,4hr

Umit Selvitopu  —  Landing Rocket  —  Logs

178 total hours
148 total cad hours
30 total pcb hours

30 total cad hours after and including May 18
30 total PCB hours after and including May 18
60 total hours after and including May 18

8/22/24 - 4h
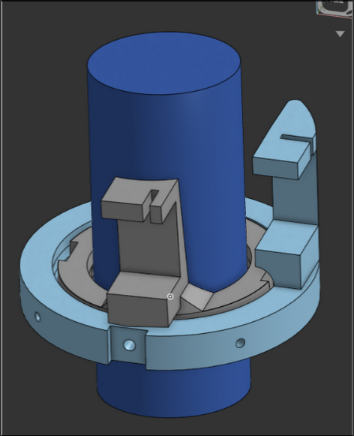
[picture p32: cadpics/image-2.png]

I made the basic geometry of the onion-style gimbal.

8/23/24 - 4h
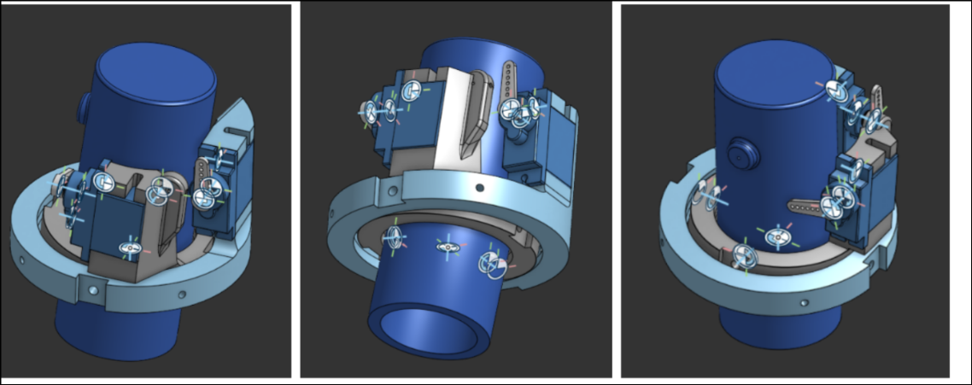
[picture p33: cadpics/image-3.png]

I refined the shape of the gimbal, added curves, and added servos. 

8/24/24 - 2h
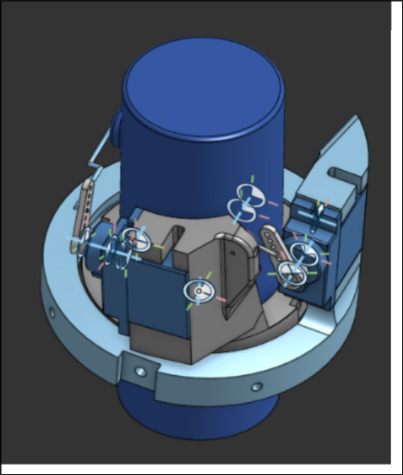
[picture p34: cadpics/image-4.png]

I added the rods for the servo

8/26/24 - 2h
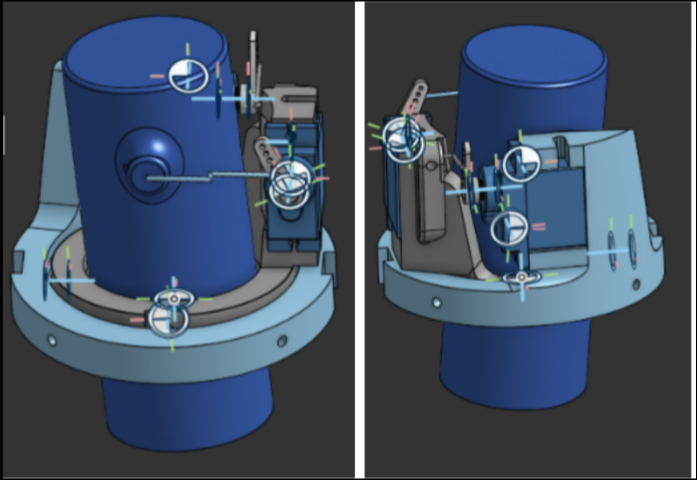
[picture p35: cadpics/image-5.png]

I added curves and chamfers to strengthen the parts and prevent bending

8/27/24 - 20min
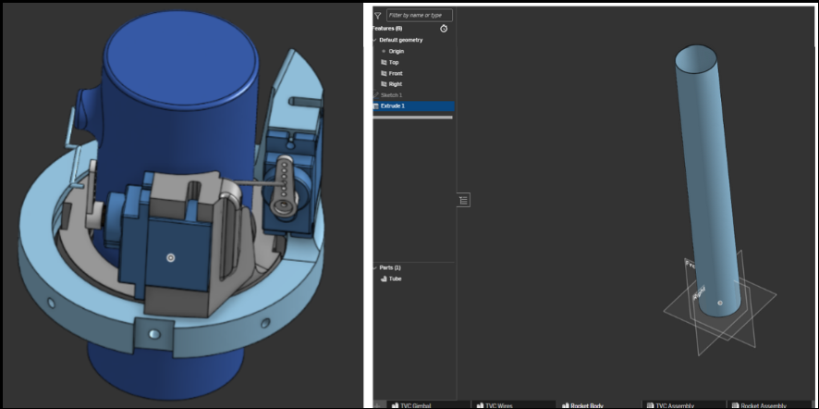
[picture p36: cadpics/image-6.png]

I started organizing the main assembly of the whole rocket

9/29/24 - 1.5h
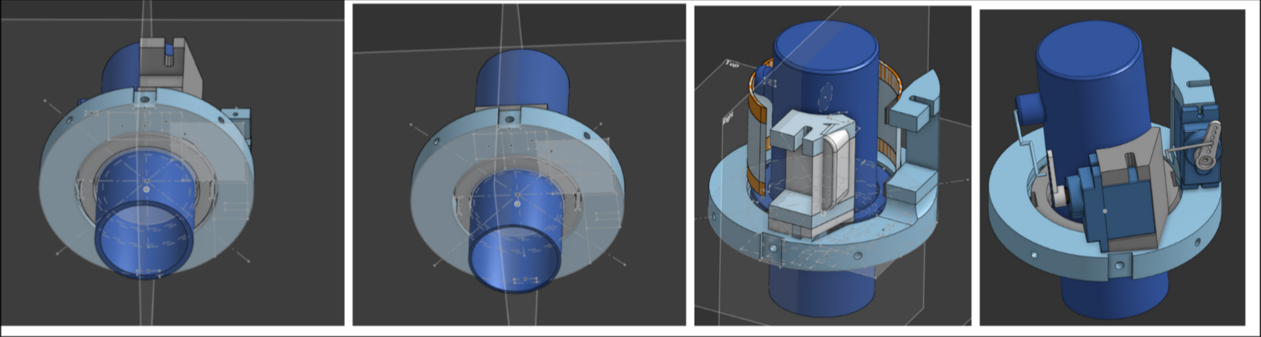
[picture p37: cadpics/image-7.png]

I messed up the geometry of the gimbal trying to edit the master sketch, so I decided to split up the master sketch into multiple sketches to make it easier to edit and select the faces from the sketches

10/6/24 - 3h
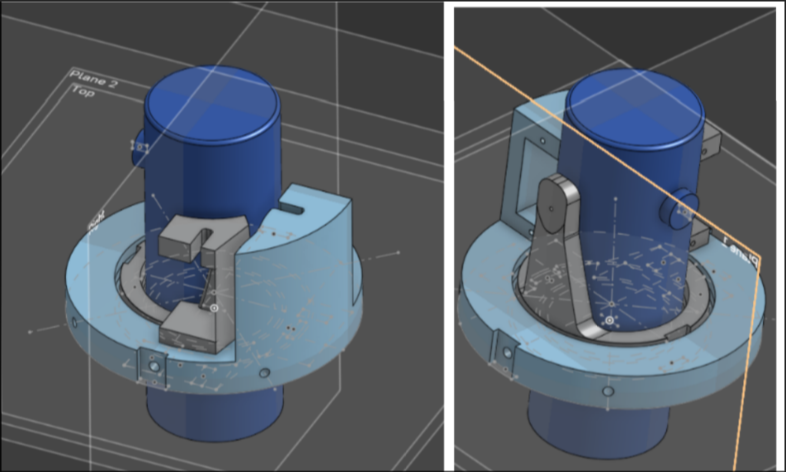
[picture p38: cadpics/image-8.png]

I realized that if I swapped the direction of the servo on the outermost gimbal slice, it would be easier to integrate. To that end, I made a place for the outer servo rod to connect to. I made that change and also edited the formatting a bit.

10/12/24 - 4h
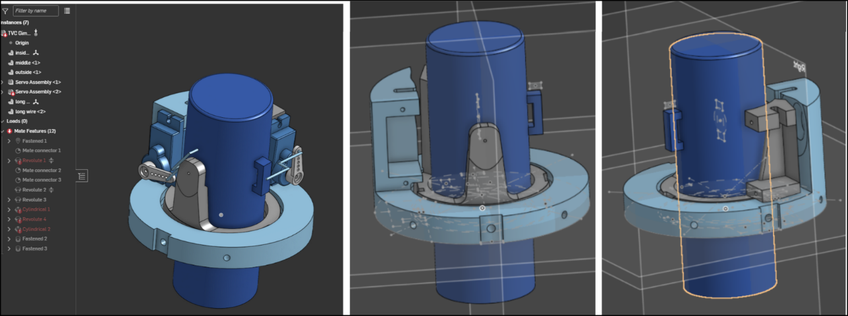
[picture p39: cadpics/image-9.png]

I changed the innermost gimbal slice to have a better rod connection. I also made a cutout in the outermost gimbal to allow the middle slice maximum range of motion. I also lowered the servos, dropping the placement of the middle gimbal slice rod holder to accommodate this optimization. I also made the servo holder in the middle slice cooler. The assembly broke.

10/13/24 - 3h
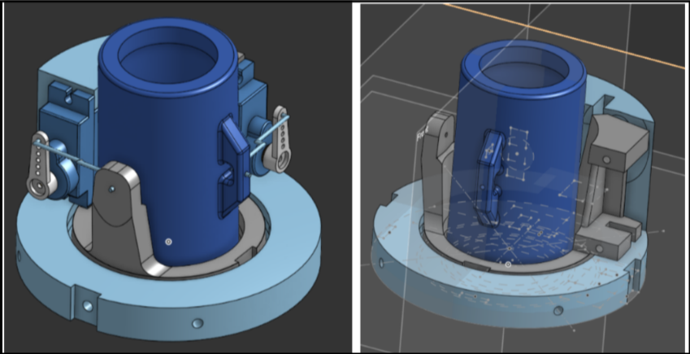
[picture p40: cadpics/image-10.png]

I refined the shape of the inner slice rod holder, adjusted the rod shapes, added fillets, and fixed the assembly that was broken. I also added a hole to the top of the inner gimbal.

10/14/24 - 3h
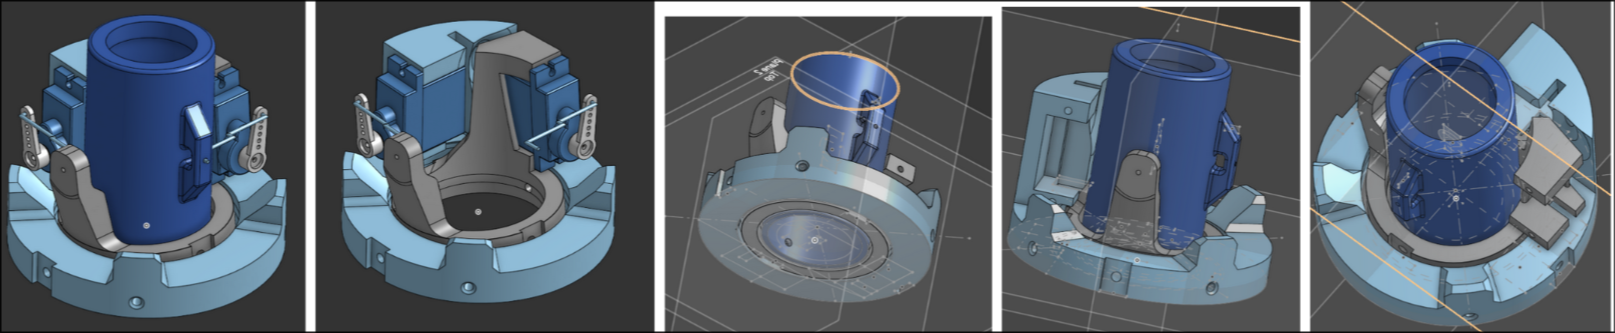
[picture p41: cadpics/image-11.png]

I refined the rod holder of the middle slice and added a channel for the servo. I also added more fillets and the side supports on the outer gimbal slice. 

11/3/24 - 2h
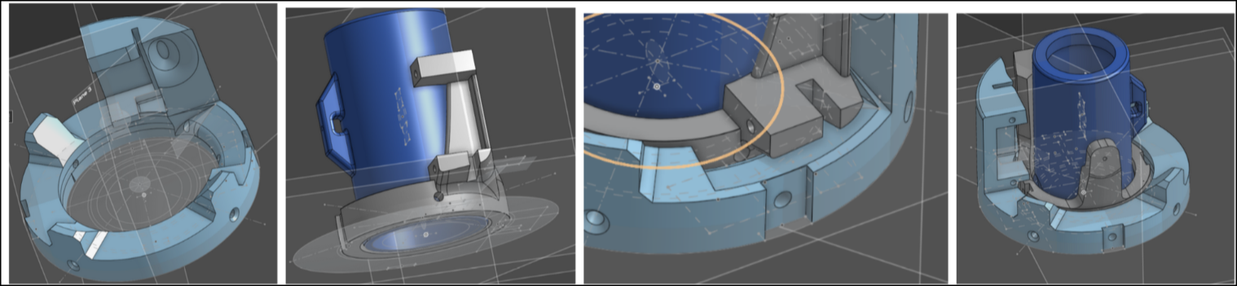
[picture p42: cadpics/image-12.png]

I added material to the bottom side of the middle slice right under the servo and cut out some from the outer slice to prevent bending.

11/7/24 - 1h
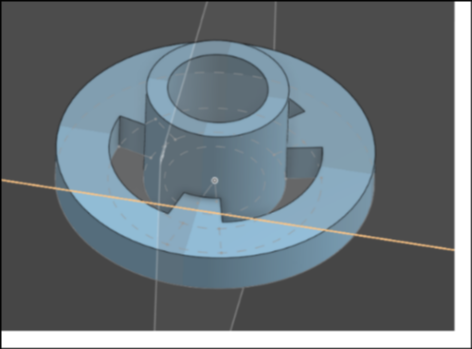
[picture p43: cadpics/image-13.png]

Got measurements from a motor I had and started making the reaction wheel.

11/8/24 - 4h
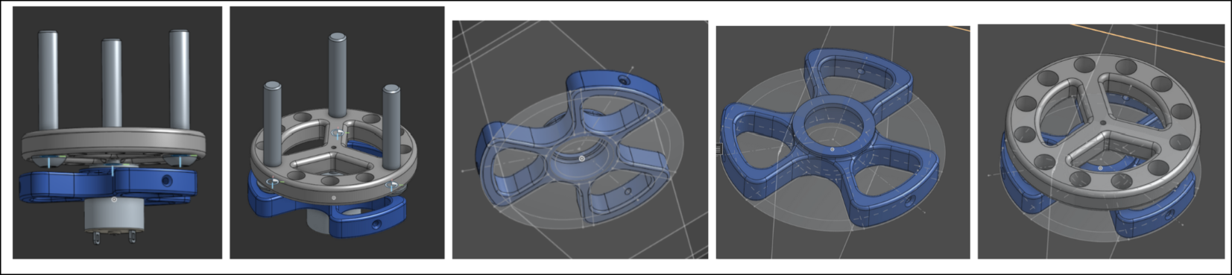
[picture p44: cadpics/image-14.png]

Got more measurements and worked on the reaction wheel.

11/9/24 - 1h
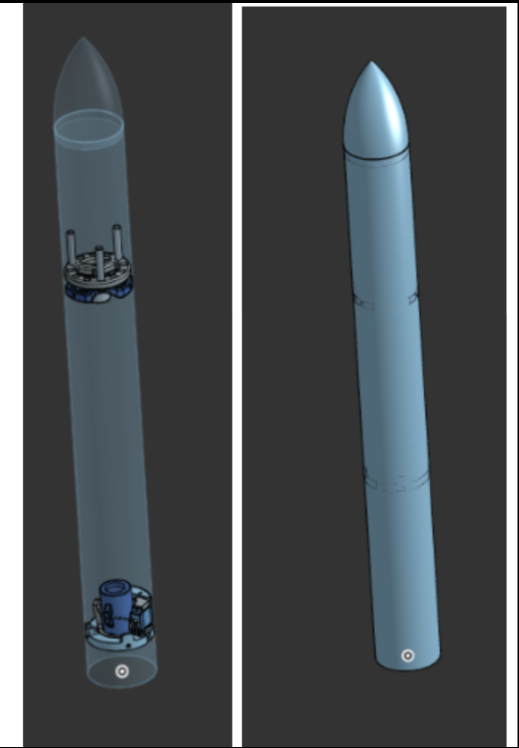
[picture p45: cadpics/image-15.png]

I made the nosecone and put everything into a full assembly. The gimbal and reaction wheel are draggable.

11/11/24 - 2h
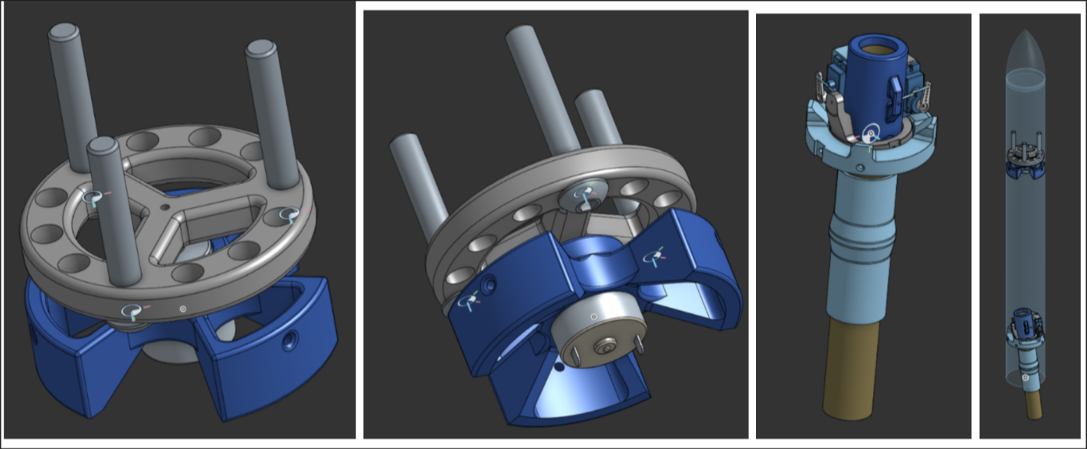
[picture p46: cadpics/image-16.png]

I made the reaction wheel stronger, added in the rocket motors, and made a connector piece to connect the two rocket motors.

2/28/25 - 3h

I did some heavy organization, putting everything into folders. I also started version 2 of the gimbal, a more optimized version. Gimbal 1 did 5 degrees in each direction, but I wanted gimbal 2 to do as much as possible. I also wanted gimbal 2 to be more parametric so when I want to change a dimension, it would be easy.

3/4/25 - 1h

I created the top-down outline of the gimbal 2 and created an assembly for it.

3/5/25 - 6h

I started adding onto the outer ring of the gimbal. I also spent a lot of time researching servo motors for the gimbal and found BMS127wv+ to be a good option. It has a 2 us dead bandwidth, can provide a lot of torque, is very fast, and is not too expensive. I imported the servo and its dimensions. I couldn't find the servo arm, so I decided to leave it until the servo is bought to model it myself. I also added a table of values to easily change major dimensions and provide a more parametric setup.

3/6/25 - 6h

Ok, this was overkill, but using the table and wanted angle of max rotation, I created a parametric area box that showed the maximum reach of the gimbal. I made this because I wanted to model the rest off of the extension of the inside gimbal and prevent it from overlapping while maximizing the limited space. I also added to the outer ring of the gimbal. 

3/7/25 - 3.5h

I added the outer ring servo and the place where its rod would connect to. I optimized it by being close to but not touching the extension area of the inner ring of the gimbal. 

3/12/25 - 5h

I changed the holder for the outer ring servo and created the holder for the middle ring servo. Also created the bearing holes, created an indent to have the middle and outer ring not overlap, and placed both servos in the right places. 

3/13/25 - 4h

I added what I guessed to be the shape of the servo arm; the dimensions are derived from a horn I found on Amazon.

3/14/25 - 1h

Worked on the incline in between the servos and added some fillets/chamfers.

3/25/25 - 4h

I decided to attach the PCB directly to the gimbal, so I extended the outer ring up and connected it to a flat place. I added a place for the wires to go through. In addition, I added holes to attach it to the cardboard airframe. A rocket motor is also added, and the middle ring of the gimbal has an extra addition to hold the bearing in more securely. 

4/17/25 - 5h

I added A PLETHORA OF 1mm FILLETS and chamfers, which produced a lot of errors that I had to fix.

4/20/25 - 4h

I added EVEN MORE FILLETS, as well as a detachable flight computer mount. More fillets inside the wiring path and under the servo of the middle ring.

4/22/25 - 3h

Added more fillets, as well as a rod added to make sure it doesn't go over the 3in max diameter. More rounding on the middle ring for strength. 

4/23/25 - 1h

Adjusted hole sizes and optimized some measurements.

4/24/25 - 1.5h

Changed some fillet dimensions and added some fillets.

4/25/25 - 30min

Edited some fillets

4/28/25 - 2h

Edited some more fillets and added face blends

4/29/25 - 1h

Even more fillet editing

4/30/25 - 4h

Optimized some more on the inner and middle rings. Broke the assembly. Started the clamper, which is a thrust reversal system that will block exhaust jets to throttle the solid rocket motors.

5/1/25 - 4h

Added some more optimization by cutting out another hole on the inner ring and more fillets. Continued designing the clamper as well

5/6/25 - 2h

Added holes, screws, and bearings.

5/7/25 - 2h

Added inlet to prevent overlap, cutout to make servo able to go in, and more optimization changes.

5/8/25 - 3h

Decided to switch to a rod format, added rod placement holes for the fuselage, merged the tvc system and flight computer mount, removed unnecessary holes.

5/9/25 - 1h

Added support rods to hold the fuselage

5/14/25 - 1h

Added that channel for the wires and adjusted some fillets.

5/15/25 - 5h

Completely scrapped the old reaction wheel and made a new one, this time more optimized and accommodated to the rod system. It is weighed down with a number of screws

5/16/25 - 4h

Added a reaction wheel motor, started the master height scratch for basically all heights of the rocket, and created the first of the snap-on outside 3D-printed parts.

5/17/25 - 4h

Played with the aesthetics, created the shape of the nose cone, and added the shell part to most of the rocket.

5/18/25 - 30min

More adjustments to colors and materials.

5/22/25 - 45min

Started landing leg sketch; started the tube for the bottom part.

5/24/25 - 2h

Organized files and experimented with different style set screws from mcmastercarr; decided on these shorter ones.

5/25/25 - 4h

Designed the landing leg system, incorporating 3D-printed pieces at the ends of the rods for hinges, additions to the outer TVC ring, and the middle of the vertical body rod. Changed to polymaker LW PLA black color. 

5/27/25 - 20min

Fixed the bend angle of the landing legs.

5/30/25 - 10min

Changed shell color to match Polymaker LW PLA white.

6/16/25 - 5h

Added McMaster-Carr syringes as dampers to the landing legs. I also added a triangle-shaped stopper to the bottom legs and a rounded end to it.

6/17/25 - 5h

I made the outer legs extend further out to prevent overlap. This was particularly annoying because of the sheer amount of fillets I had to experiment with and add to get it to look good and have structural integrity. I added a servo to the 3dp part on the middle of the body to deploy the landing legs. 

6/18/25 - 5h

I created the shell parts for the full length of the rocket, cutting out holes where the deployment servo is and the other features. I modeled it so that there were no unnecessary gaps or inconsistencies.

7/1/25 - 3h

I added these stoppers. These took some time to get right, as mirroring/rotational patterning didn't work for this addition. I also boolean cut out some overlaps in the shell pieces.

7/8/25 - 1h

Despite it being less aerodynamic like this, I made the nose cone pointy for aesthetic purposes.

7/12/25 - 30h


I made this flight computer for the final project for a CS class and independent CS study at my school. 7/12/25 is the submission date. I worked on it in class and out of class. I created the schematic and the PCB, although I still need to refine some aspects of both. Reading though the datasheets and selecting the parts took a decent amount of time.

7/18/25 - 3h

Added cutouts for the rubber band to go through and connection points to connect.

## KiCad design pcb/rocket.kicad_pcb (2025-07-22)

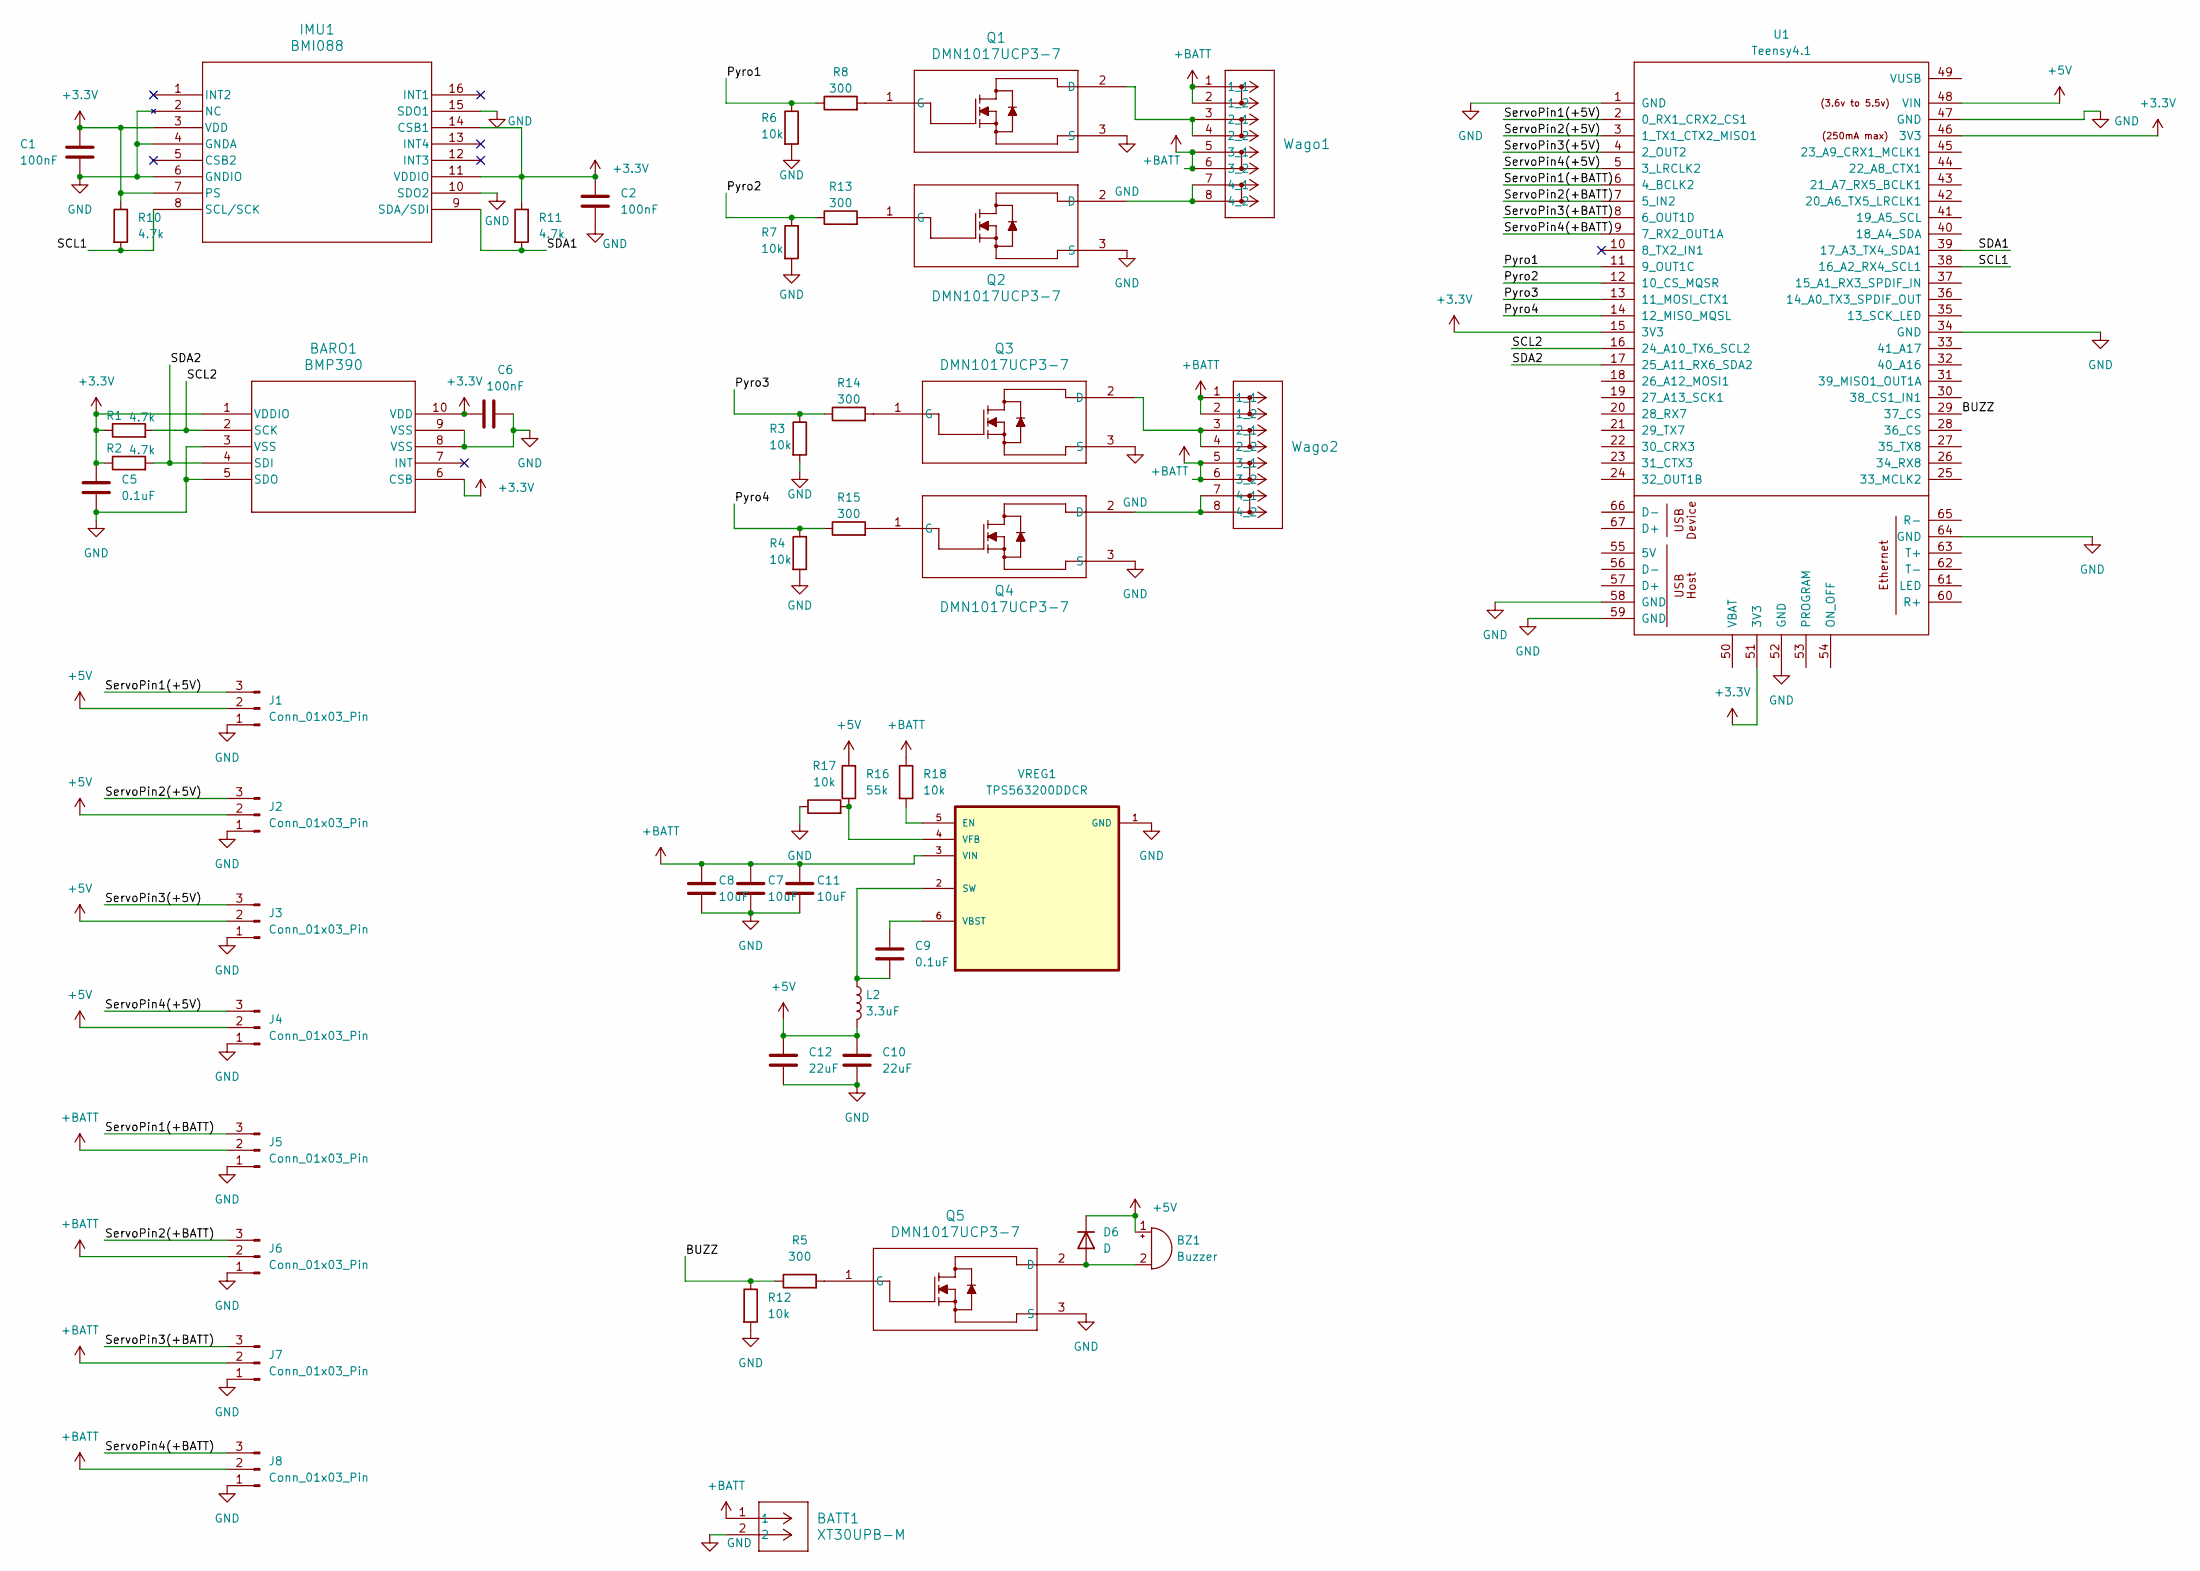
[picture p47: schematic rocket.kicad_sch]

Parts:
BARO1: BMP390; 10LGA_2X2X0p75_BOS
BATT1: XT30UPB-M; CONN_XT30UPB-M_AMA
BZ1: Buzzer; CEM-1206S_CUD
C1, C2, C6: 100nF; C_0805_2012Metric
C5, C9: 0.1uF; C_0805_2012Metric
C7, C8, C11: 10uF; C_0805_2012Metric
C10, C12: 22uF; C_0805_2012Metric
D6: D; D_0805_2012Metric
IMU1: BMI088; QFN_BMI085_BOS
J1, J2, J3, J4, J5, J6, J7, J8: Conn_01x03_Pin; PinHeader_1x03_P2.54mm_Vertical
L2: 3.3uF; IND_NRS5030_TAY
Q1, Q2, Q3, Q4, Q5: DMN1017UCP3-7; X3-DSN1010-3_DIO
R1, R2, R10, R11: 4.7k; R_0805_2012Metric
R3, R4, R6, R7, R12, R17, R18: 10k; R_0805_2012Metric
R5, R8, R13, R14, R15: 300; R_0805_2012Metric
R16: 55k; R_0805_2012Metric
U1: Teensy4.1; Teensy41
VREG1: TPS563200DDCR
Wago1, Wago2: 2601-1104; CONN4_2601-1104_WAG

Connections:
+3.3V: BARO1.1 (VDDIO), BARO1.6 (CSB), BARO1.10 (VDD), C1.1, C2.1, C5.1, C6.2, IMU1.3 (VDD), IMU1.7 (PS), IMU1.11 (VDDIO), IMU1.14 (CSB1), R1.1, R2.1, R10.1, R11.1, U1.15 (3V3), U1.46 (3V3), U1.51 (3V3)
+5V: BZ1.1 (+), C10.2, C12.2, D6.1 (K), J1.2, J2.2, J3.2, J4.2, L2.2, R16.2, U1.48 (VIN)
+BATT: BATT1.1, C7.1, C8.1, C11.1, J5.2, J6.2, J7.2, J8.2, R18.1, VREG1.3 (VIN), Wago1.1 (1_1), Wago1.2 (1_2), Wago1.5 (3_1), Wago1.6 (3_2), Wago2.1 (1_1), Wago2.2 (1_2), Wago2.5 (3_1), Wago2.6 (3_2)
/BUZZ: R5.1, R12.1, U1.29 (37_CS)
/Pyro1: R6.1, R8.1, U1.11 (9_OUT1C)
/Pyro2: R7.1, R13.1, U1.12 (10_CS_MQSR)
/Pyro3: R3.1, R14.1, U1.13 (11_MOSI_CTX1)
/Pyro4: R4.1, R15.1, U1.14 (12_MISO_MQSL)
/SCL1: IMU1.8 (SCL/SCK), R10.2, U1.38 (16_A2_RX4_SCL1)
/SCL2: BARO1.2 (SCK), R1.2, U1.16 (24_A10_TX6_SCL2)
/SDA1: IMU1.9 (SDA/SDI), R11.2, U1.39 (17_A3_TX4_SDA1)
/SDA2: BARO1.4 (SDI), R2.2, U1.17 (25_A11_RX6_SDA2)
/ServoPin1(+5V): J1.3, U1.2 (0_RX1_CRX2_CS1)
/ServoPin1(+BATT): J5.3, U1.6 (4_BCLK2)
/ServoPin2(+5V): J2.3, U1.3 (1_TX1_CTX2_MISO1)
/ServoPin2(+BATT): J6.3, U1.7 (5_IN2)
/ServoPin3(+5V): J3.3, U1.4 (2_OUT2)
/ServoPin3(+BATT): J7.3, U1.8 (6_OUT1D)
/ServoPin4(+5V): J4.3, U1.5 (3_LRCLK2)
/ServoPin4(+BATT): J8.3, U1.9 (7_RX2_OUT1A)
GND: BARO1.3 (VSS), BARO1.5 (SDO), BARO1.8 (VSS), BARO1.9 (VSS), BATT1.2, C1.2, C2.2, C5.2, C6.1, C7.2, C8.2, C10.1, C11.2, C12.1, IMU1.2 (NC), IMU1.4 (GNDA), IMU1.6 (GNDIO), IMU1.10 (SDO2), IMU1.15 (SDO1), J1.1, J2.1, J3.1, J4.1, J5.1, J6.1, J7.1, J8.1, Q1.3 (S), Q2.3 (S), Q3.3 (S), Q4.3 (S), Q5.3 (S), R3.2, R4.2, R6.2, R7.2, R12.2, R17.1, U1.1 (GND), U1.34 (GND), U1.47 (GND), U1.52 (GND), U1.58 (GND), U1.59 (GND), U1.64 (GND), VREG1.1 (GND)
unnamed: BZ1.2 (-), D6.2 (A), Q5.2 (D)
unnamed: Q1.2 (D), Wago1.3 (2_1), Wago1.4 (2_2)
unnamed: Q1.1 (G), R8.2
unnamed: Q2.2 (D), Wago1.7 (4_1), Wago1.8 (4_2)
unnamed: Q2.1 (G), R13.2
unnamed: Q3.2 (D), Wago2.3 (2_1), Wago2.4 (2_2)
unnamed: Q3.1 (G), R14.2
unnamed: Q4.2 (D), Wago2.7 (4_1), Wago2.8 (4_2)
unnamed: Q4.1 (G), R15.2
unnamed: Q5.1 (G), R5.2
unnamed: R18.2, VREG1.5 (EN)
unnamed: C9.2, L2.1, VREG1.2 (SW)
unnamed: C9.1, VREG1.6 (VBST)
unnamed: R16.1, R17.2, VREG1.4 (VFB)

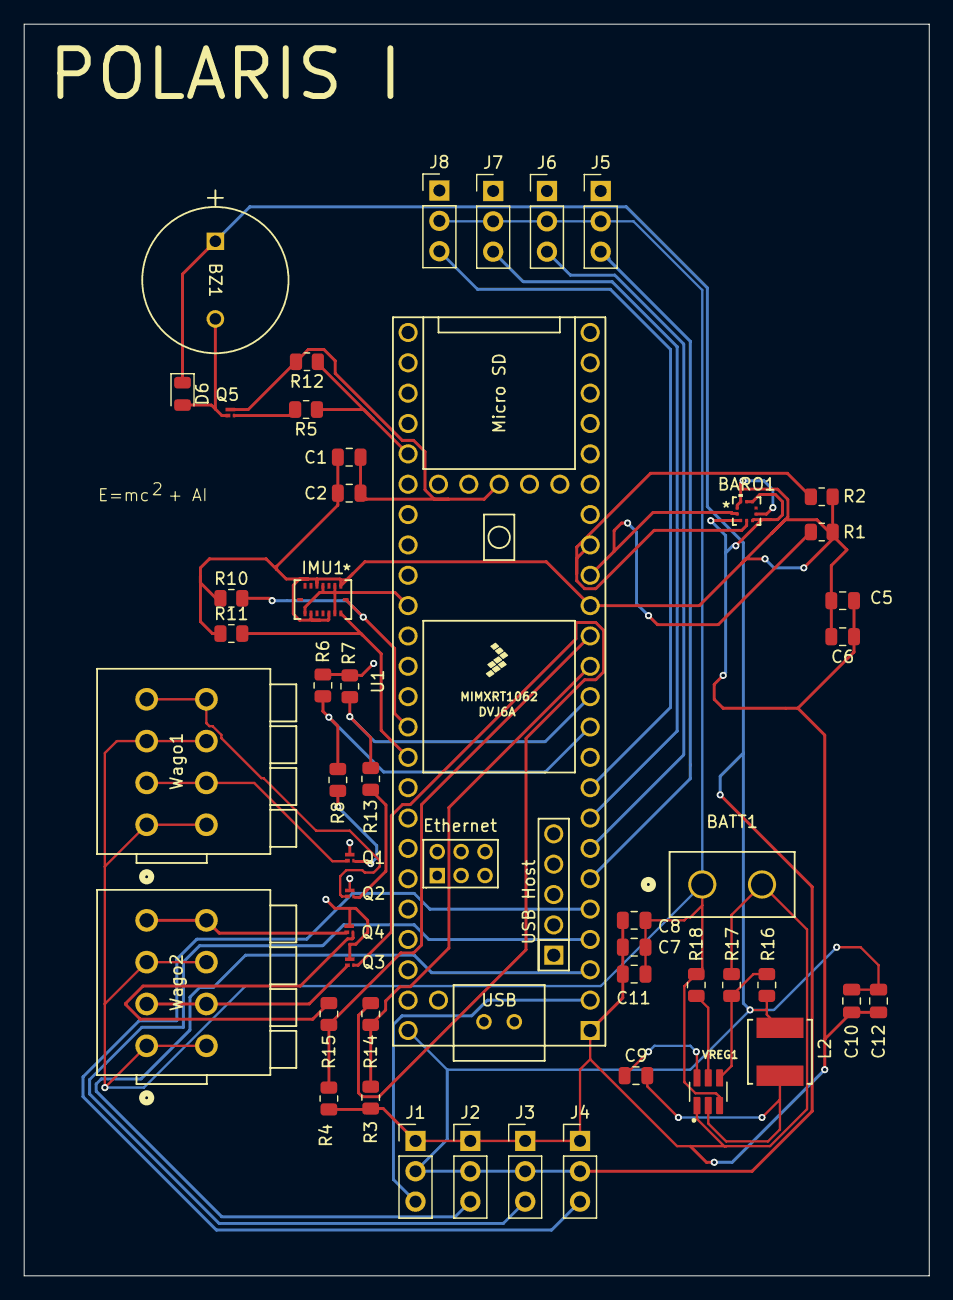
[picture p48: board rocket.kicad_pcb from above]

Board: 2 copper layers, 75.8 x 104.8 mm, 50 parts (0 on the bottom side), 35 nets.

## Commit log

2025-07-22 add readme
    [bom.csv]
2025-07-22 fix bom
    [bom.csv]
2025-07-22 add kicad files
    [rocket.kicad_pcb, rocket.kicad_sch]
2025-07-23 add markdown bom
2025-07-23 move markdown bom
2025-07-23 add cad journal
2025-07-23 add cad image
2025-07-23 fix cad and pcb images
2025-07-23 add acetyl copolymer rods to bom
2025-07-23 add rods to bom
    [bom.csv]
2025-07-23 add BOM cost
2025-07-23 add cad
    [Assembly - 7510A651_Plastic Syringe (1).step, Assembly - 7510A651_Plastic Syringe (10).step, Assembly - 7510A651_Plastic Syringe (11).step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]
2025-07-23 add servos
    [bom.csv]
2025-07-24 update bom
    [rocket.kicad_pcb, rocket.kicad_sch]
